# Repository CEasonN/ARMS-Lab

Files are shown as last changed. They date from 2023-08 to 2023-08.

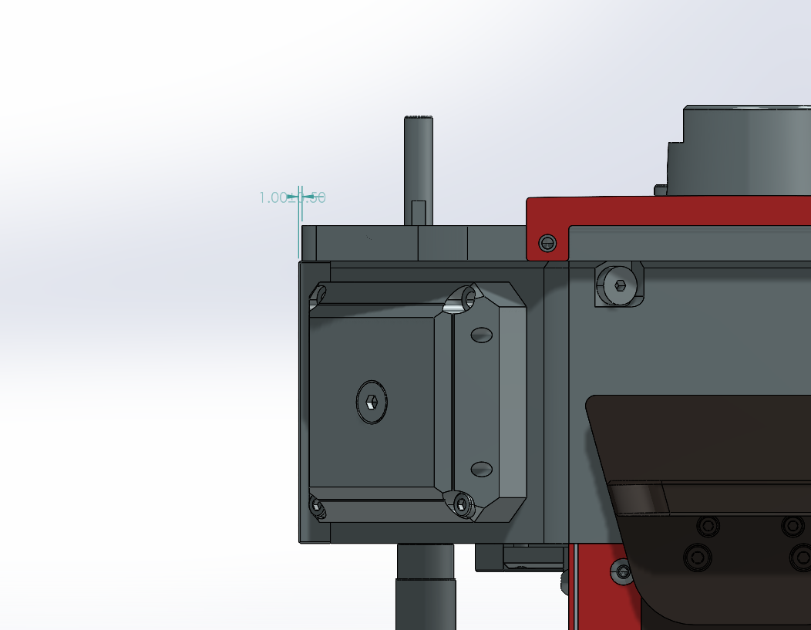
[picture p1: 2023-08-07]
SW screenshot/Annotation 2023-03-12 135321.png

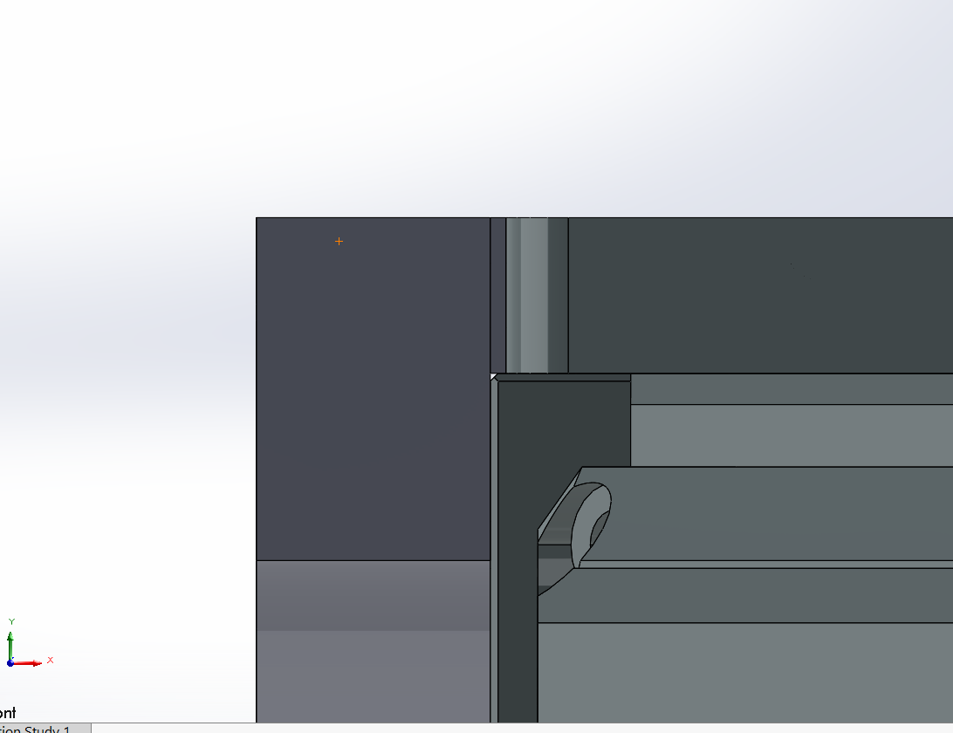
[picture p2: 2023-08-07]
SW screenshot/Annotation 2023-03-12 181023.png

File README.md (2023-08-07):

# ARMS-Lab
This experiment revolves around a height offset monitoring camera that records the directed energy deposition process. After the camera was installed, our graduate researchers observed some distortion in the camera’s images. They suspected that the distortion occurs as the heat from the deposition accumulates in the camera and its mounting apparatus.
Therefore, our objective is to characterize and quantify the heat transfer into the camera using an approximation for the clad temperature and clad area. We will then use these calculations to determine a failure condition for the camera and identify its critical component along with its thermal limit. Finally, we will validate our calculations by attaching thermocouples to the camera and conducting a circular deposition until a steady state response is reached. This constant heat addition will allow us to investigate a worst-case scenario for the camera. If necessary, a thermal management solution will be designed and implemented to mitigate overheating.

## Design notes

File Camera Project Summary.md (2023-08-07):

Height control camera thermal management project

# Summary
- Assess and characterize overheating problem on the the height control camera during maximum power continuous deposition.  
- Design and implement a minimum-complexity thermal management solution. 
- Validate solution performance under nominal conditions.

Secondary goal:
- Design enclosure for new IR raspberry pi camera
- Validate thermal performance under nominal conditions

# Resources to Start
- [height control methodology overview]("\ARMS_LAB\Publishing\2021\2021 Height Controller CIRP\CIRP 2021 - Soshi et al.pdf")
- [Vivian's thesis, details about camera mount design]("\ARMS_LAB\Forms and Documents\Thesises Dissertations\Vivian_Zhou_MSI_Thesis_2021.pdf")
- any heat transfer textbook for reference
- [visual height camera datasheet just the board](http://www.elpcctv.com/low-illumination-hd-usb-camera-module-aptina-ar0130-color-sensor-p-232.html)
- [visual height camera datasheet product](http://www.webcamerausb.com/elp-4mm-manual-focus-lens-aluminum-industrial-box-housing-960p-industrial-camera-p-214.html)

# Suggested To-Do List
1. Read Vivian's thesis, understand the thermal management problem
2. Create basic heat transfer model 
	1. Estimate clad irradiance 
	2. Estimate air cooling on enclosure
	3. Find expected lens and sensor equilibrium temperature
3. Instrument camera and design heating experiment
	1. Determine how to set temperature limits
4. Compare results to model
5. Determine cooling load required to not exceed required temperature
6. Begin solution design phase

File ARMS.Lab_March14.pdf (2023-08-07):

Masakazu Soshi
University of California Davis

## EME 199 WQ 2023: Undergraduate Research

Donjel Anthony Brox
Yizheng Chen

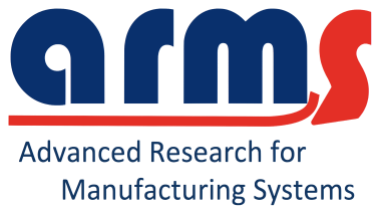
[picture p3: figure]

# Agenda

## - CCD Camera Thermal Management (CTM) Experiment - Substrate Manufacturing - Securing Current CCD Camera Fixture - New CCD Camera Fixture

# CTM Experiment: Description

## Problem:

- Current CCD camera overheats after ~170 thin-wall layers,

## causing the camera to turn off

## Solution: - Identify which part of the camera is overheating by attaching thermocouples to camera and performing depositions - Design thermal management solution to mitigate overheating

# CTM Experiment: Setup

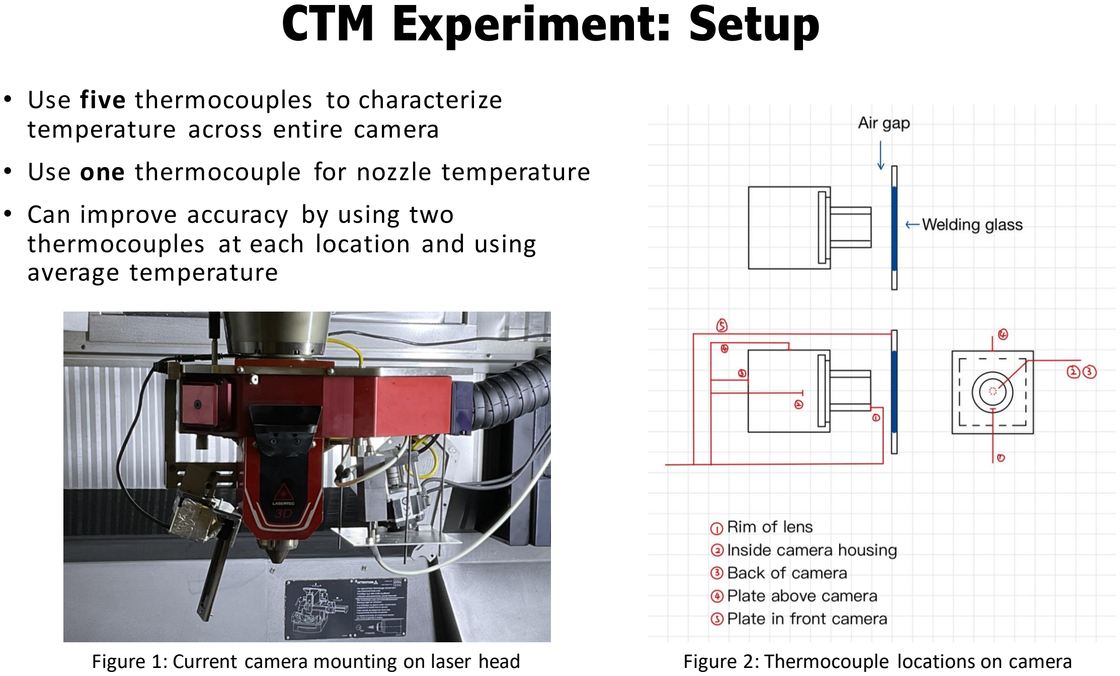
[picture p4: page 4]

- Use five thermocouples to characterize temperature across entire camera
- Use one thermocouple for nozzle temperature
- Can improve accuracy by using two thermocouples at each location and using average temperature
Figure 1: Current camera mounting on laser head | Figure 2: Thermocouple locations on camera

# CTM Experiment: Depositions

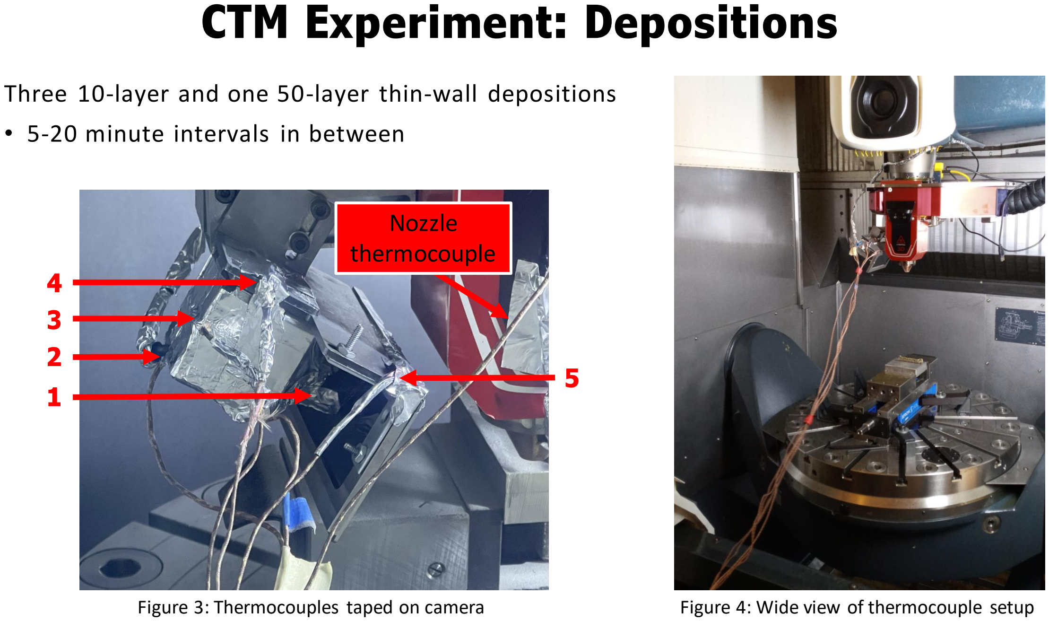
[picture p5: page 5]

Three 10-layer and one 50-layer thin-wall depositions
- 5-20 minute intervals in between
Figure 3: Thermocouples taped on camera | Figure 4: Wide view of thermocouple setup

1

3
2

4

5

Nozzle
thermocouple

# CTM Experiment: Temperature Data

Observations:
- Camera is protected by shield, but slowly heats up from shield radiating absorbed heat
- Shield temperature increases linearly then drops slowly after deposition ends
- Due to internal cooling, the nozzle has a controlled, oscillating temperature

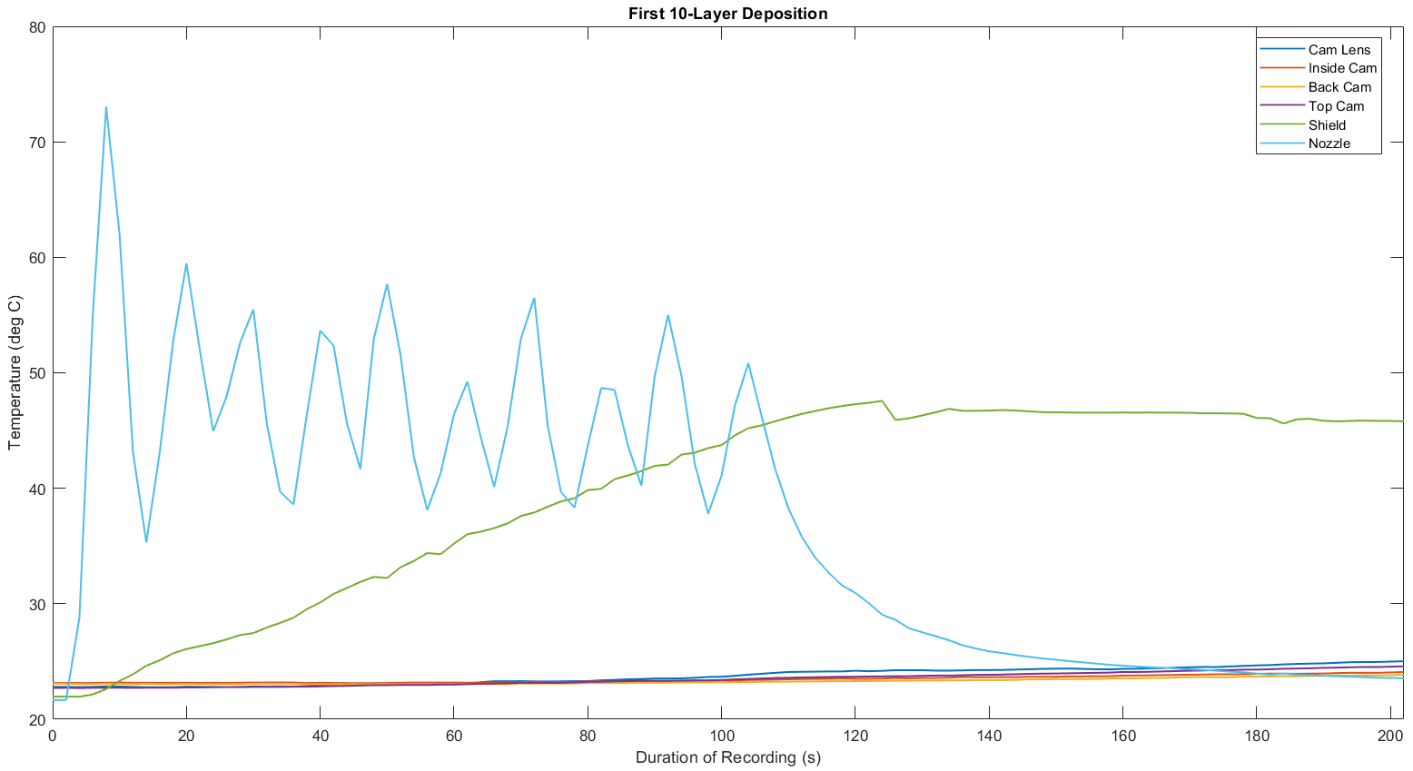
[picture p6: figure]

# CTM Experiment: Temperature Data

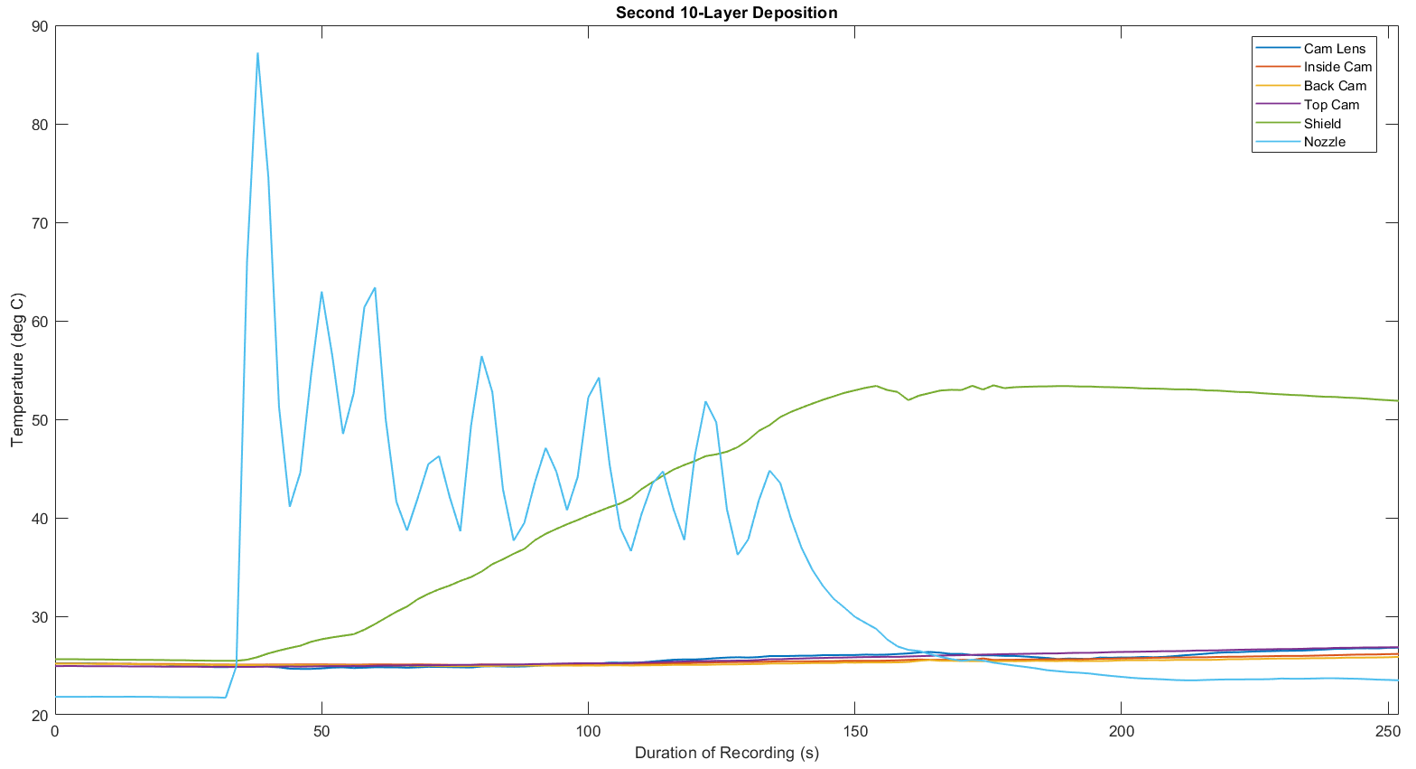
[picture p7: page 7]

# CTM Experiment: Temperature Data

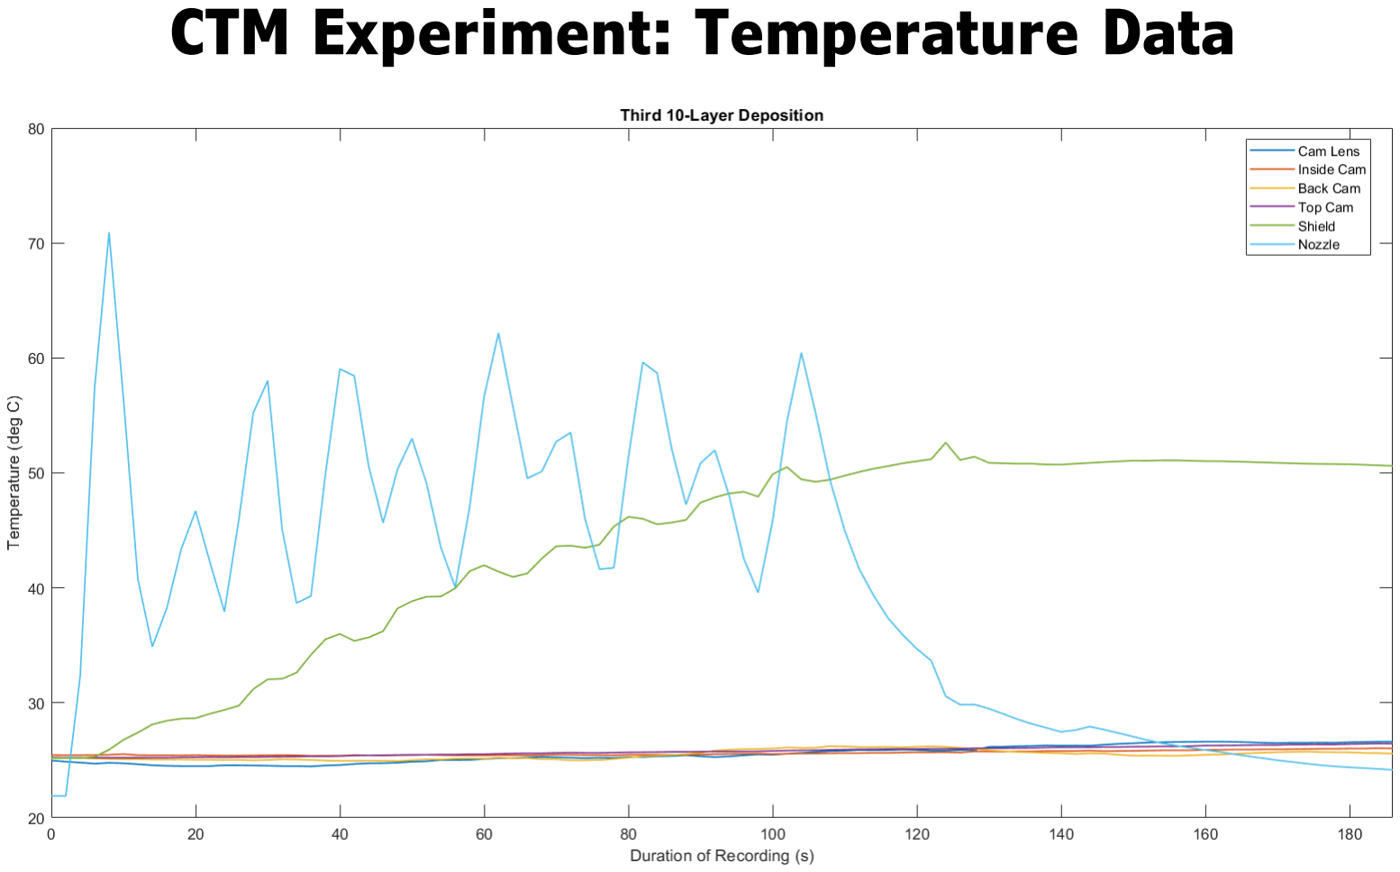
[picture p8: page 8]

Observations:
- Incomplete data for shield since DAC temperature range not set high enough
- Camera is protected by shield, but slowly heats up from shield radiating absorbed heat
- Shield temperature increases linearly then drops slowly after deposition ends
- Due to internal cooling, the nozzle has an oscillating temperature that slowly increases

# CTM Experiment: Temperature Data

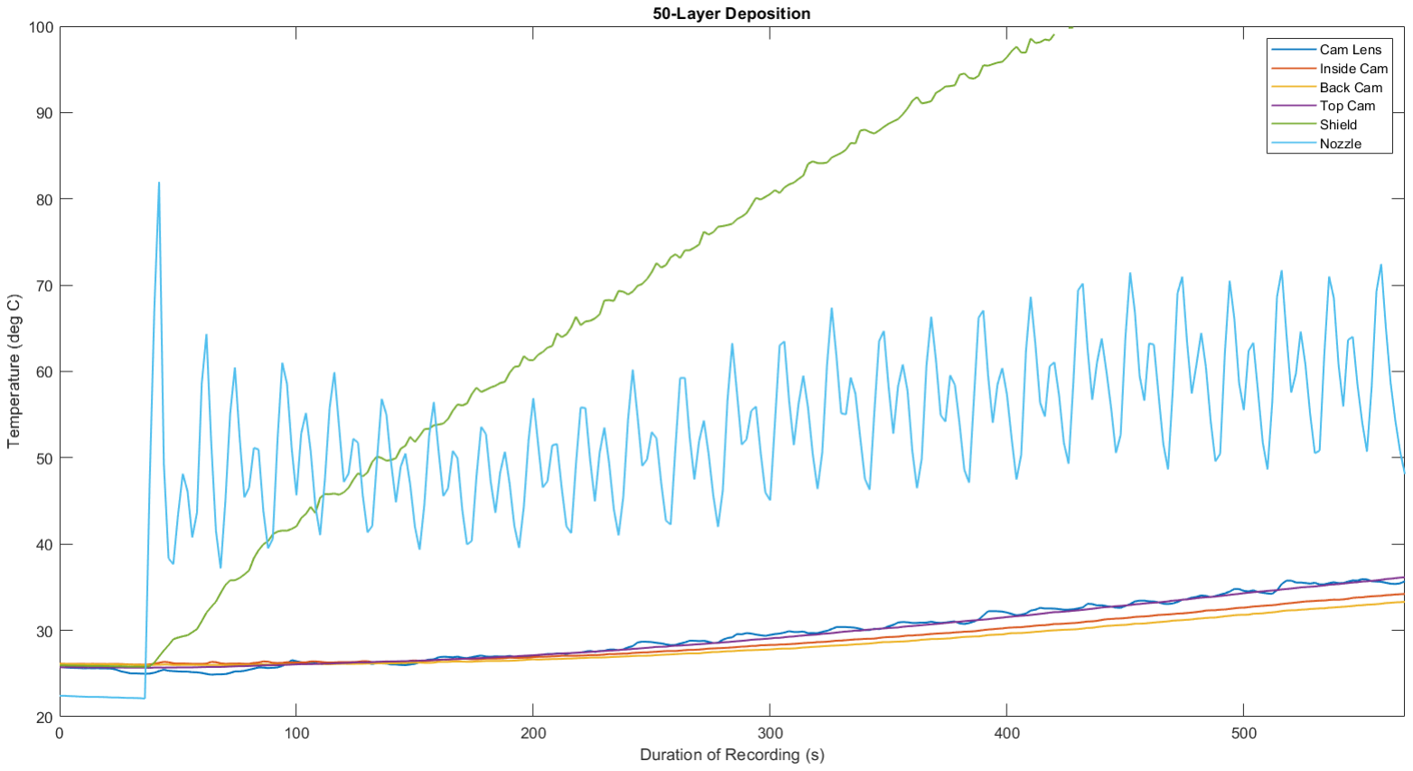
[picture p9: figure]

Observations:
- Camera slowly heats up after deposition due to shield radiating heat absorbed earlier
- Nozzle drops to room temperature quickly after deposition ends, at which point the camera is only being heated by the shield

# CTM Experiment: Temperature Data

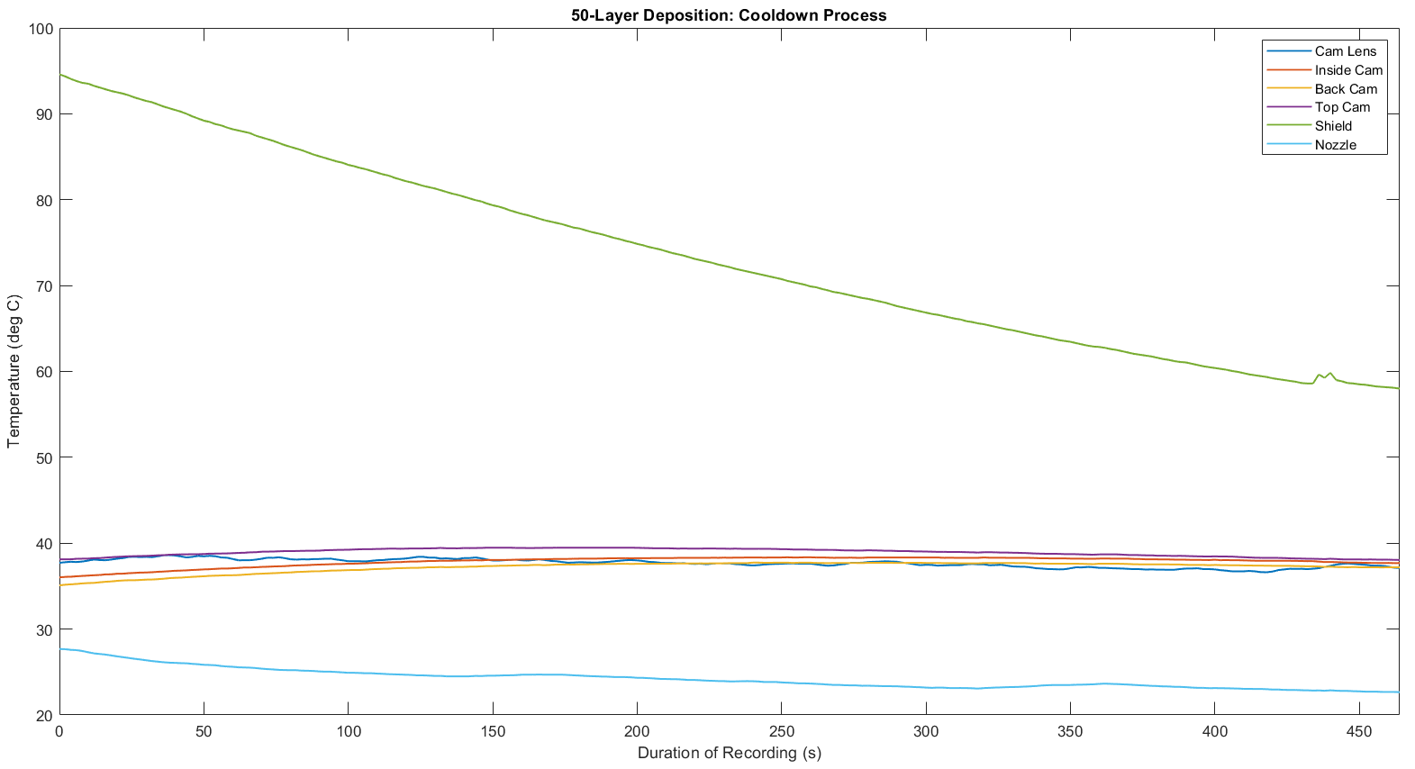
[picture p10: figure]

# CTM Experiment: Analysis

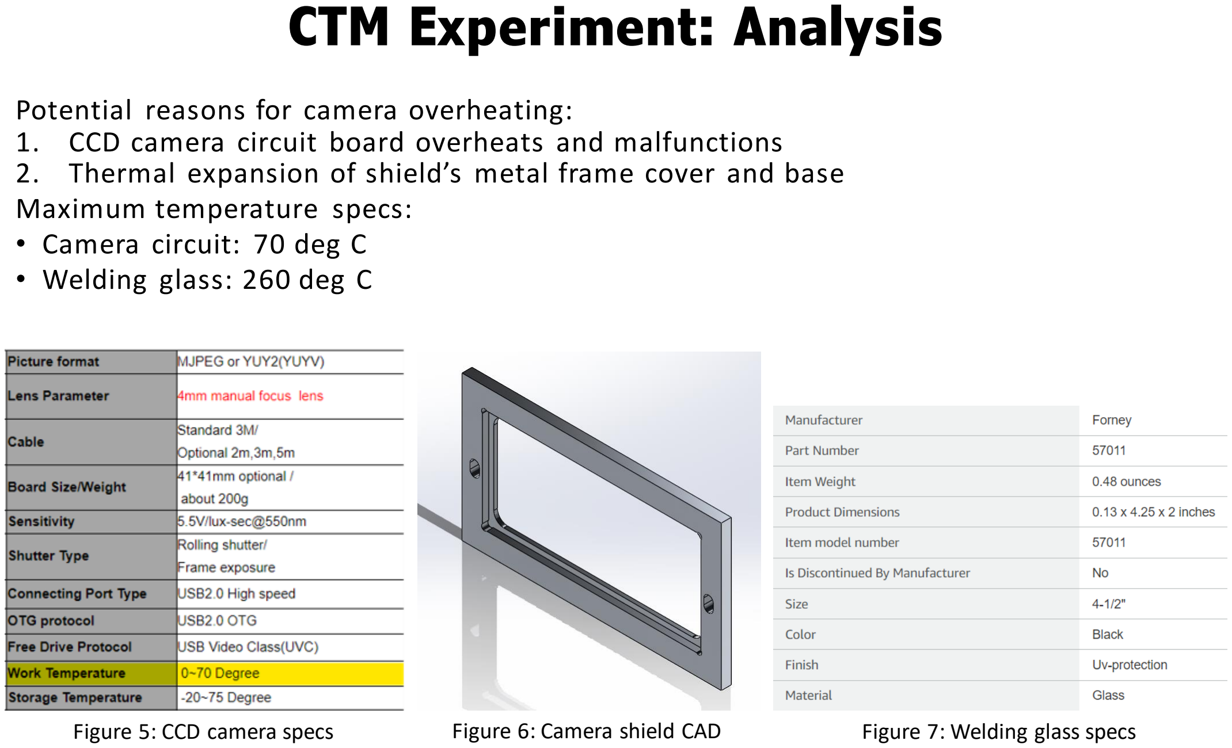
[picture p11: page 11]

Potential reasons for camera overheating:
1. CCD camera circuit board overheats and malfunctions
2. Thermal expansion of shield’s metal frame cover and base Maximum temperature specs:
- Camera circuit: 70 deg C
- Welding glass: 260 deg C
Figure 5: CCD camera specs | Figure 6: Camera shield CAD | Figure 7: Welding glass specs

## Takeaways from experimental data and equipment specs: - Use curve fitting to estimate shield and camera temperature after any number of layers

- Allows us to estimate when the camera will fail, which we’ll use to determine thermal management solution
- Among all camera thermocouples, use camera lens data for curve fitting since it reads highest temperatures and absorbs most heat

# CTM Experiment: Data Analysis

# CTM Experiment: Data Analysis

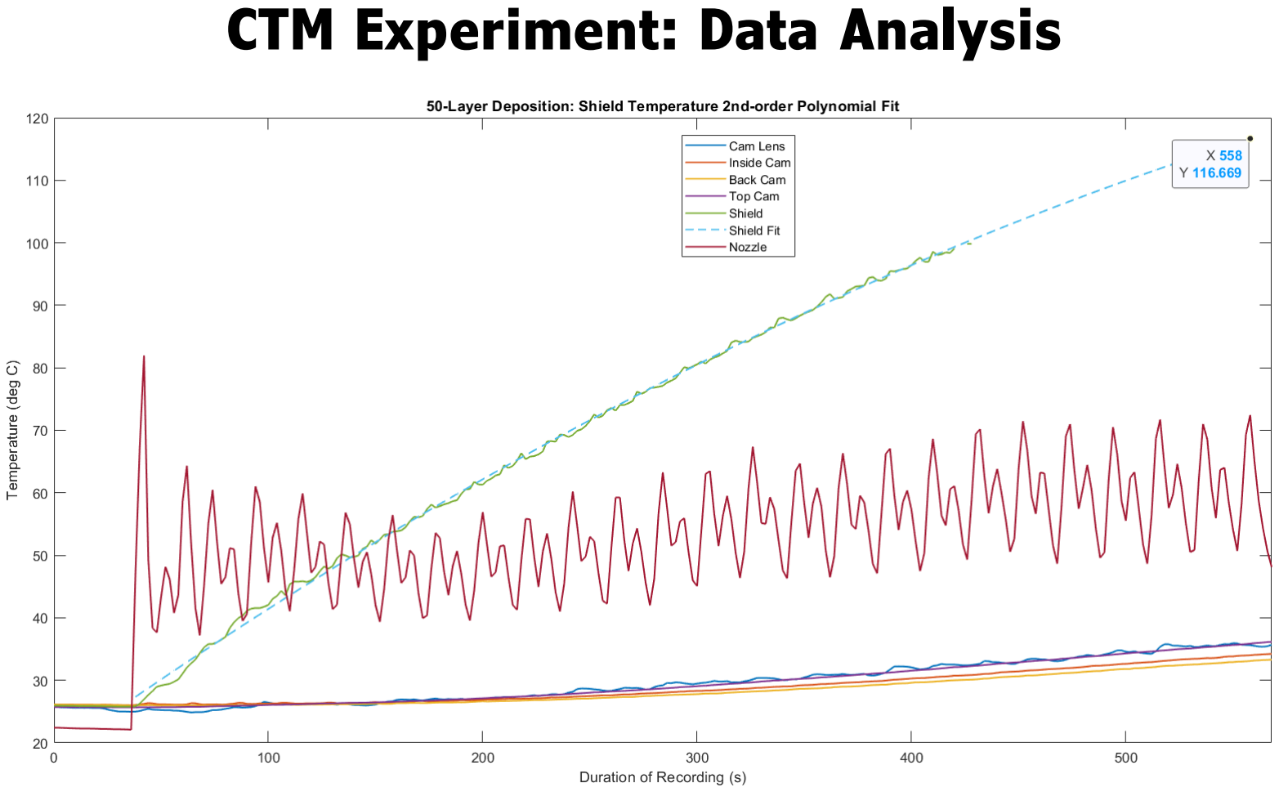
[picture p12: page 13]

The shield is predicted to have reached 116 deg C after 50 layers.

# CTM Experiment: Data Analysis

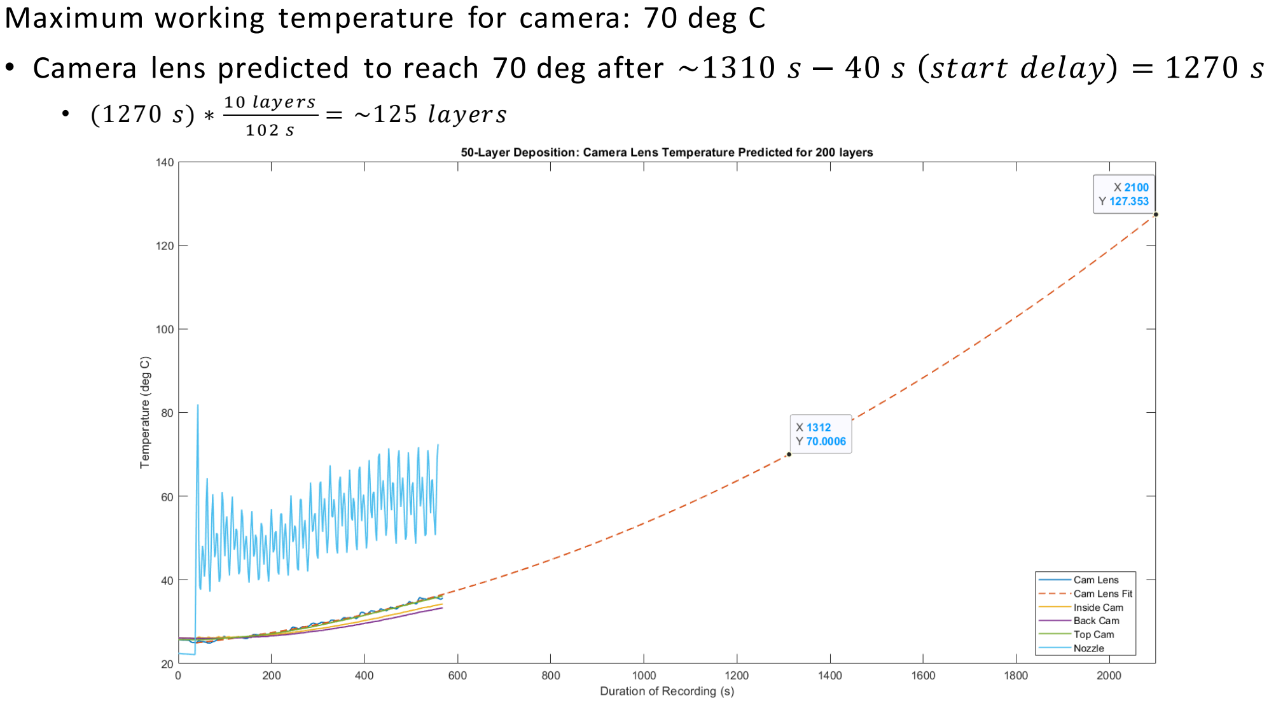
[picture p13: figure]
10 laye rs; = ~125 layers

Maximum working temperature for camera: 70 deg C
- Camera lens predicted to reach 70 deg after ~1310 s − 40 s start delay = 1270 s

Investigate whether heat sinks will suffice by quantifying theoretical heat dissipation provided
- Geometry constraints: plates above camera constrain heat sink to 129 x 36 mm area
- Optimize heat dissipation performance by developing MS Excel sheet
Investigate if a larger air gap between camera and shield provides sufficient insulation

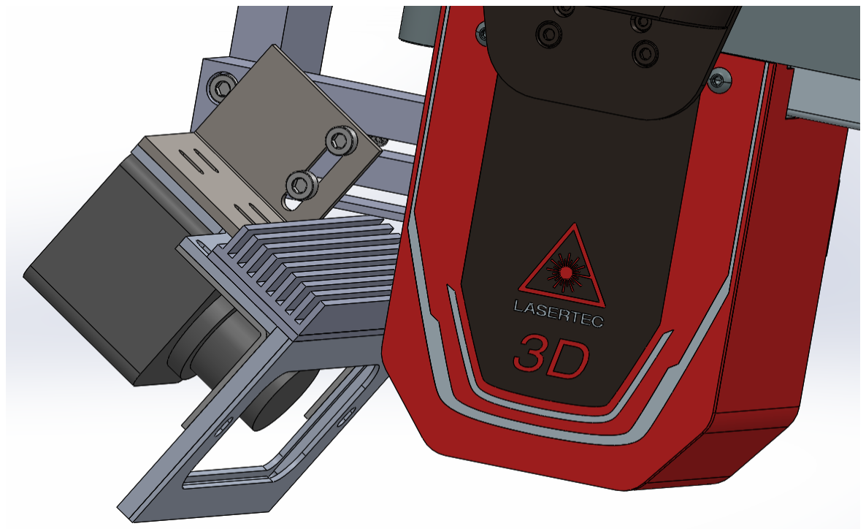
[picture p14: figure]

Figure 8: CAD draft of heat sink atop CCD camera shield

# CTM Experiment: Thermal Management

# Substrate Manufacturing

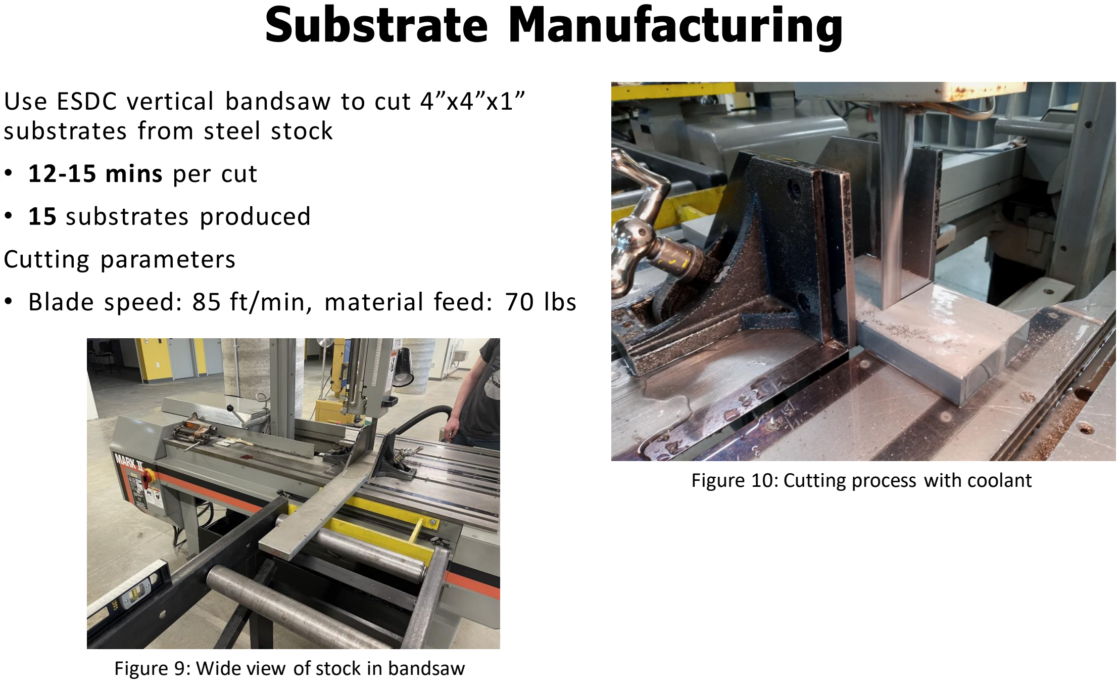
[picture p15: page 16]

Use ESDC vertical bandsaw to cut 4”x4”x1” substrates from steel stock
- 12-15 mins per cut
- 15 substrates produced
Cutting parameters
- Blade speed: 85 ft/min, material feed: 70 lbs

Figure 9: Wide view of stock in bandsaw

Figure 10: Cutting process with coolant

# Securing Current CCD Camera Fixture

Problem:
- Screwing the fixture into the laser head causes fixture to tilt, making the camera position inaccurate each time it’s installed
- Issue is due to laser head not being flush with fixture (see Figure 11)
Possible solutions:
- L-shaped metal piece
- Fixes fixture in a new plane, preventing rotation
- Thin metal spacer
- Fills the space in between the laser head and fixture, making them flush

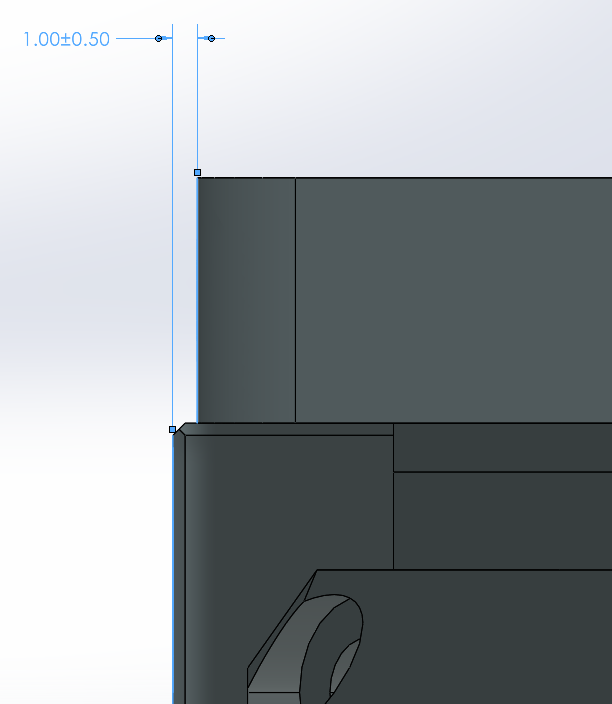
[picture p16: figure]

Figure 11: 1mm discrepancy on laser head mating face

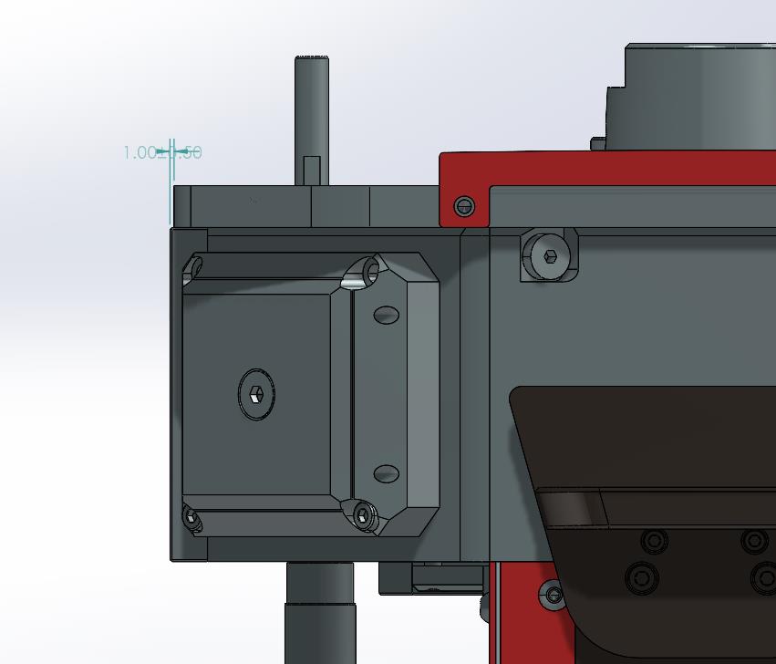
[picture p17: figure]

Figure 12: 1mm discrepancy on laser head mating face (zoomed out)

# Current CCD Camera Fixture: Spacer

# Current CCD Camera Fixture: Spacer

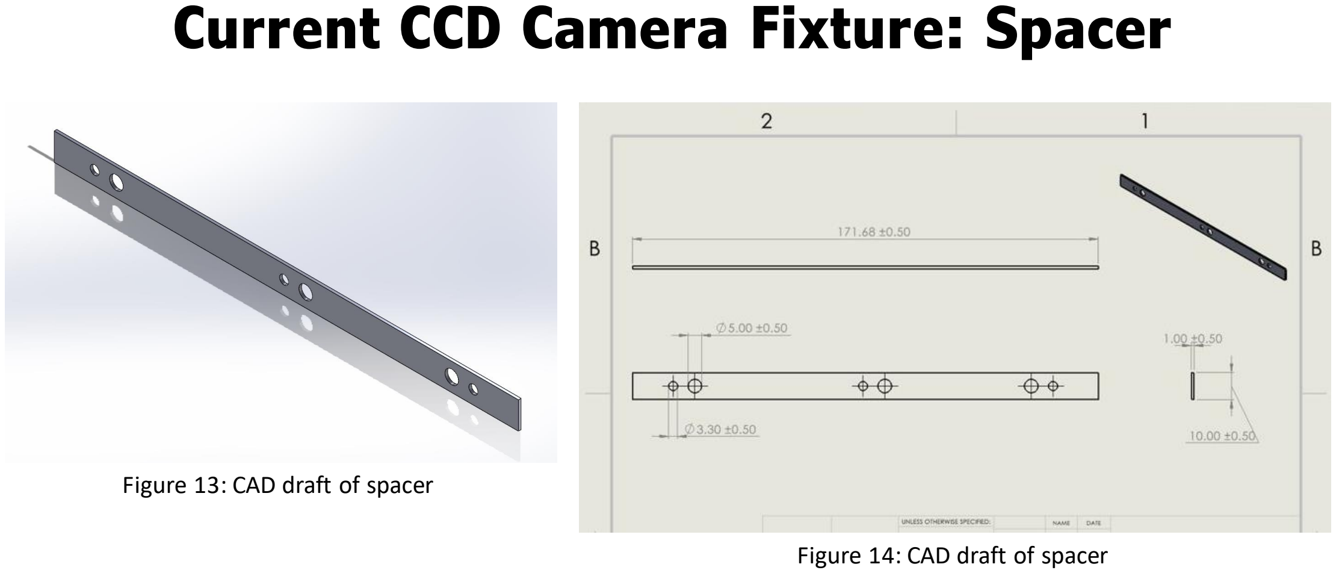
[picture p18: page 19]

Figure 13: CAD draft of spacer

Figure 14: CAD draft of spacer

# Current CCD Camera Fixture: Spacer

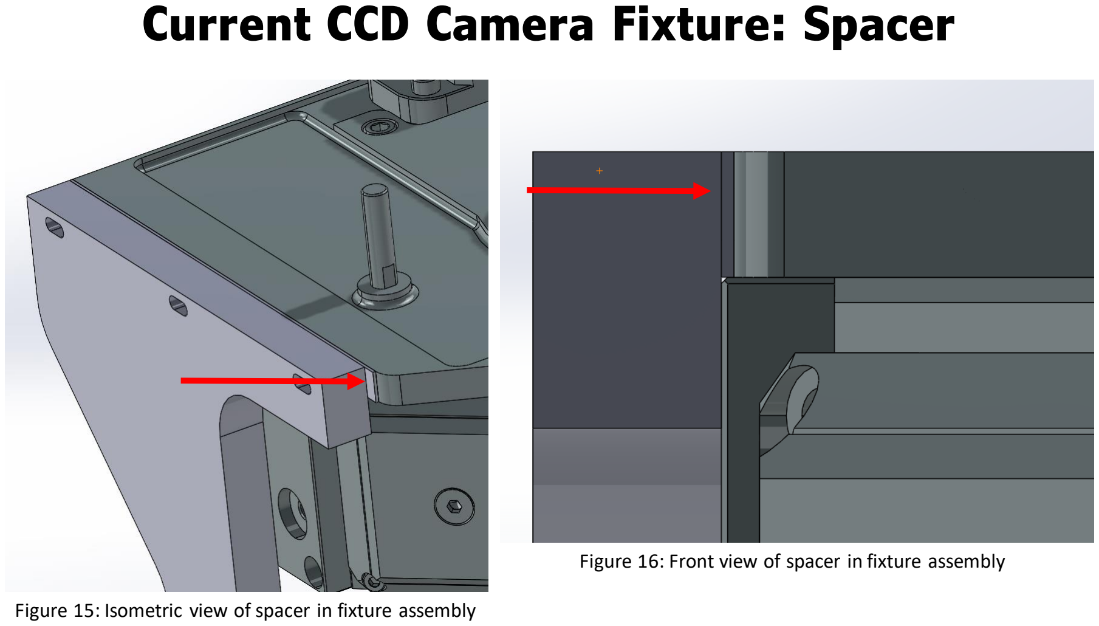
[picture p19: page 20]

Figure 15: Isometric view of spacer in fixture assembly

Figure 16: Front view of spacer in fixture assembly

# Current CCD Camera Fixture: Angle Bracket

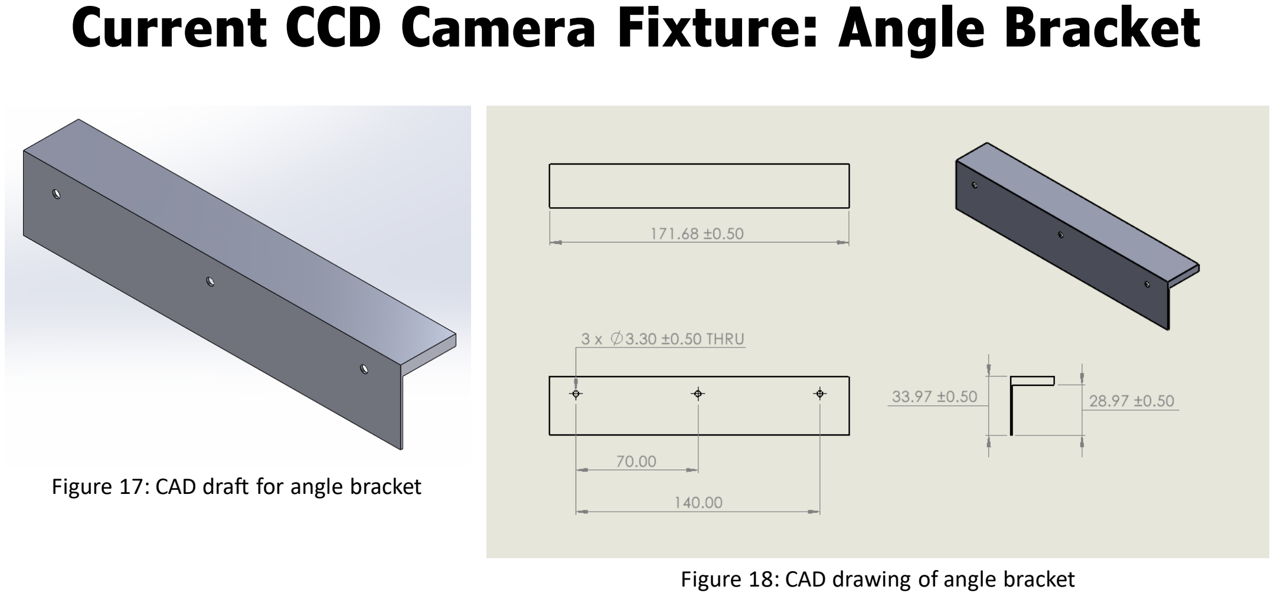
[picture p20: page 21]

Figure 17: CAD draft for angle bracket

Figure 18: CAD drawing of angle bracket

# Current CCD Camera Fixture: Angle Bracket

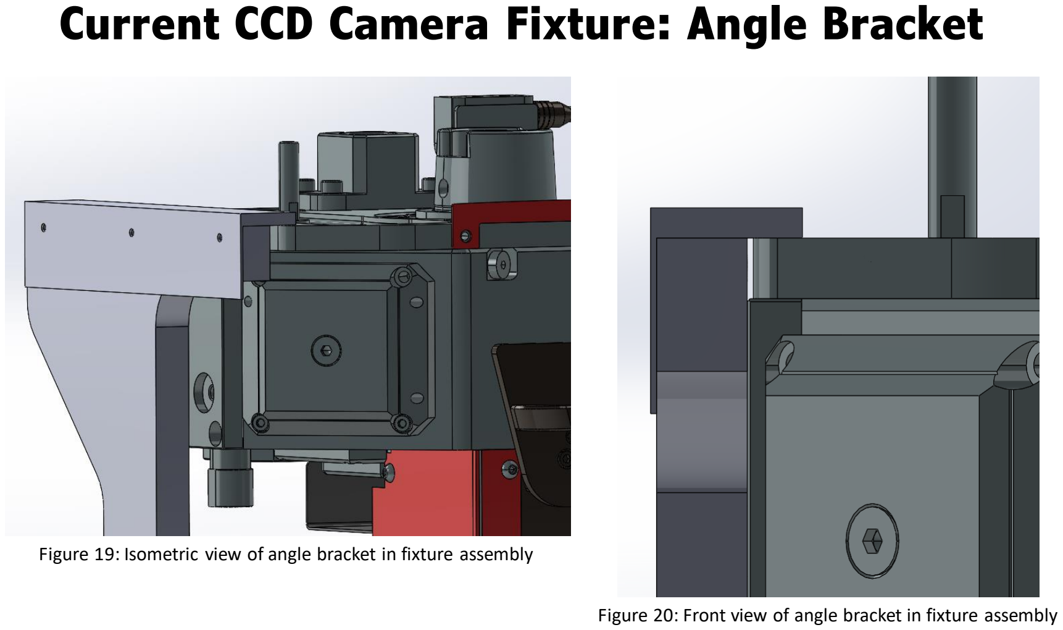
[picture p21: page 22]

Figure 19: Isometric view of angle bracket in fixture assembly

Figure 20: Front view of angle bracket in fixture assembly

# New CCD Camera Fixture: Fixture Points

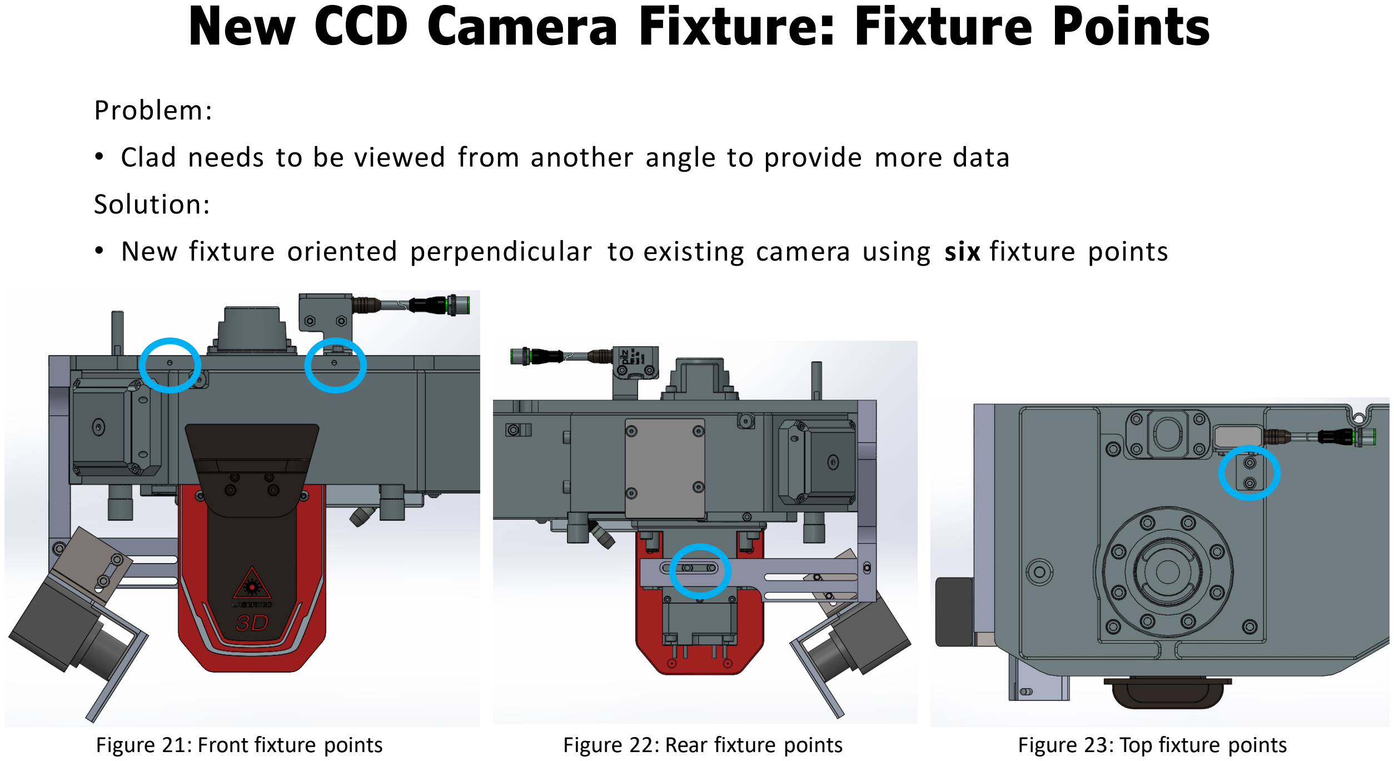
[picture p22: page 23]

Problem:
- Clad needs to be viewed from another angle to provide more data
Solution:
- New fixture oriented perpendicular to existing camera using six fixture points
Figure 21: Front fixture points | Figure 22: Rear fixture points | Figure 23: Top fixture points

# New CCD Camera Fixture: Draft Assembly

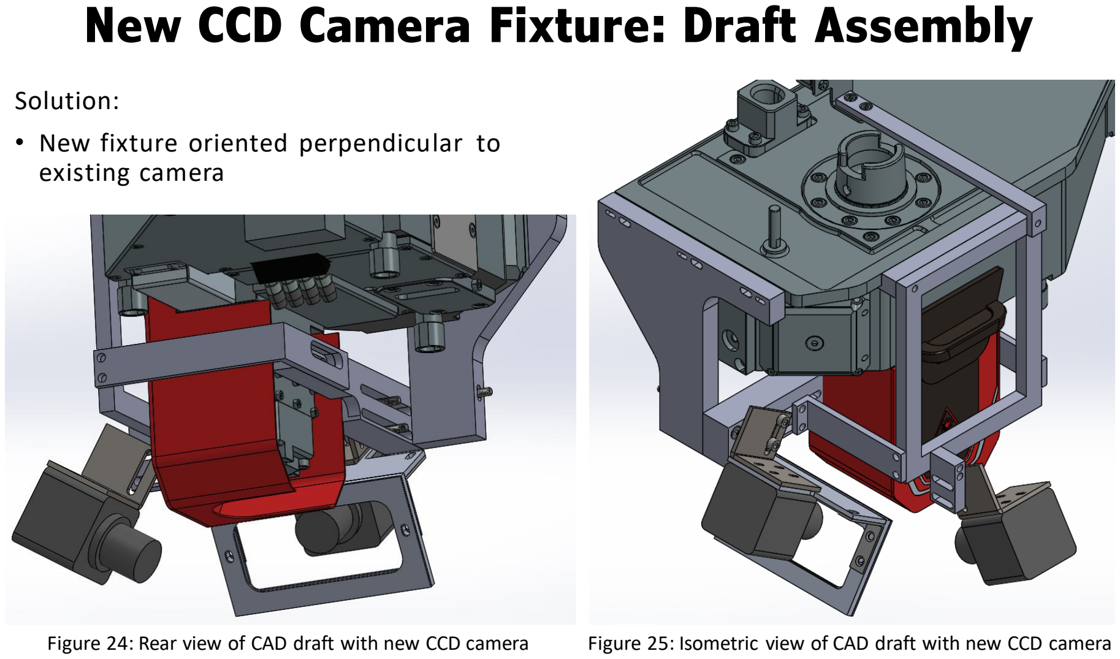
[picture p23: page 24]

Solution:
- New fixture oriented perpendicular to existing camera

Figure 24: Rear view of CAD draft with new CCD camera Figure 25: Isometric view of CAD draft with new CCD camera

# Future Work

## Experiment - Finish analysis of results

- Research properties of welding glass and temperature tolerances of camera

## - Continue designing thermal management solution - Manufacture/order and implement solution - Perform CFD and/or FEA analysis on working solution - Write report on finished solution

## Continue developing current CCD camera fixture addition and new CCD camera fixture

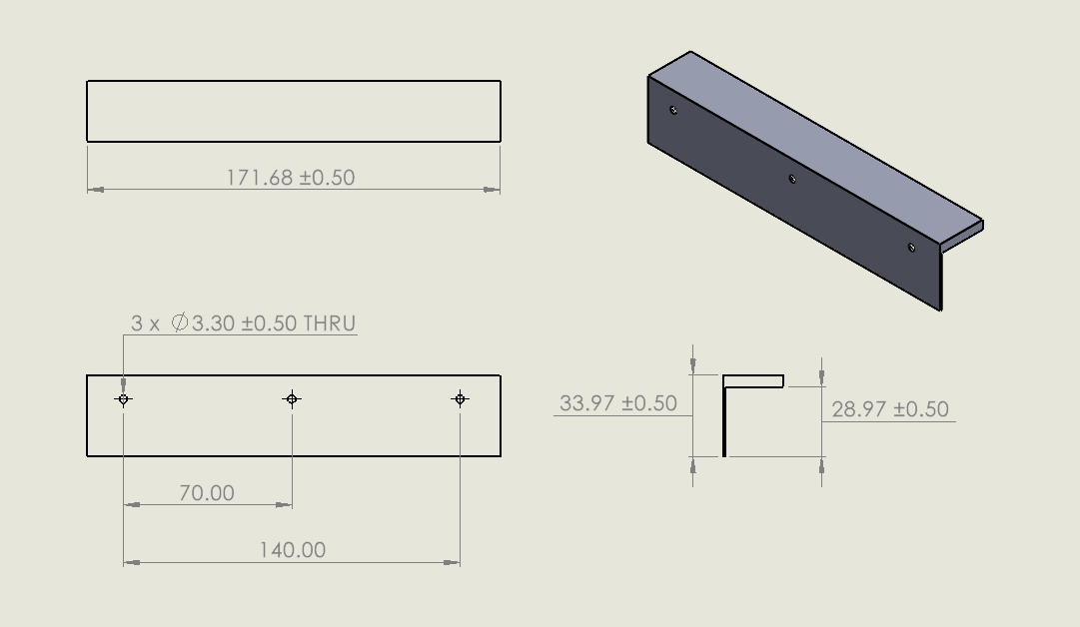
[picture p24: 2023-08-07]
SW screenshot/Annotation 2023-03-12 184950.png

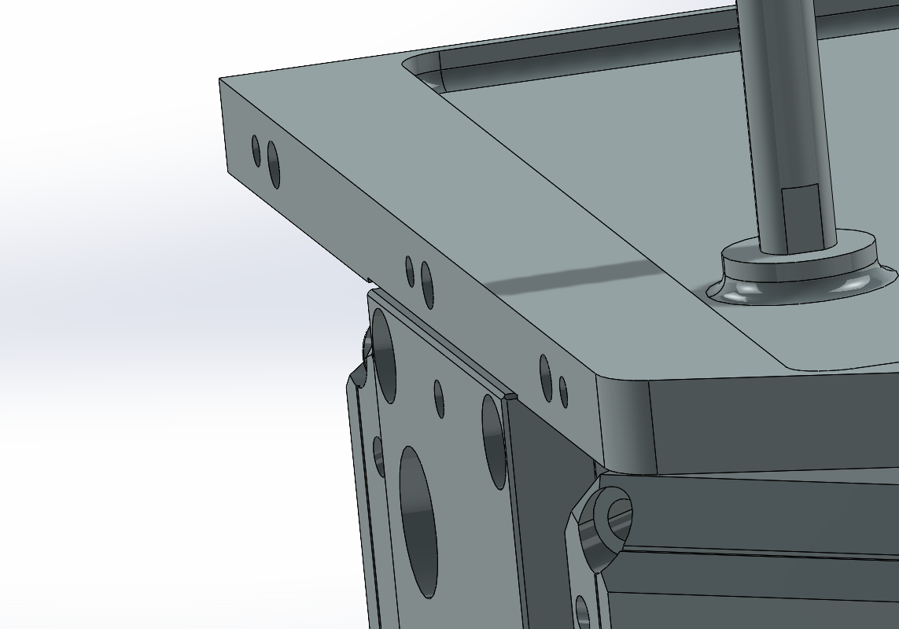
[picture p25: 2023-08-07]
SW screenshot/Annotation 2023-03-12 153420.png

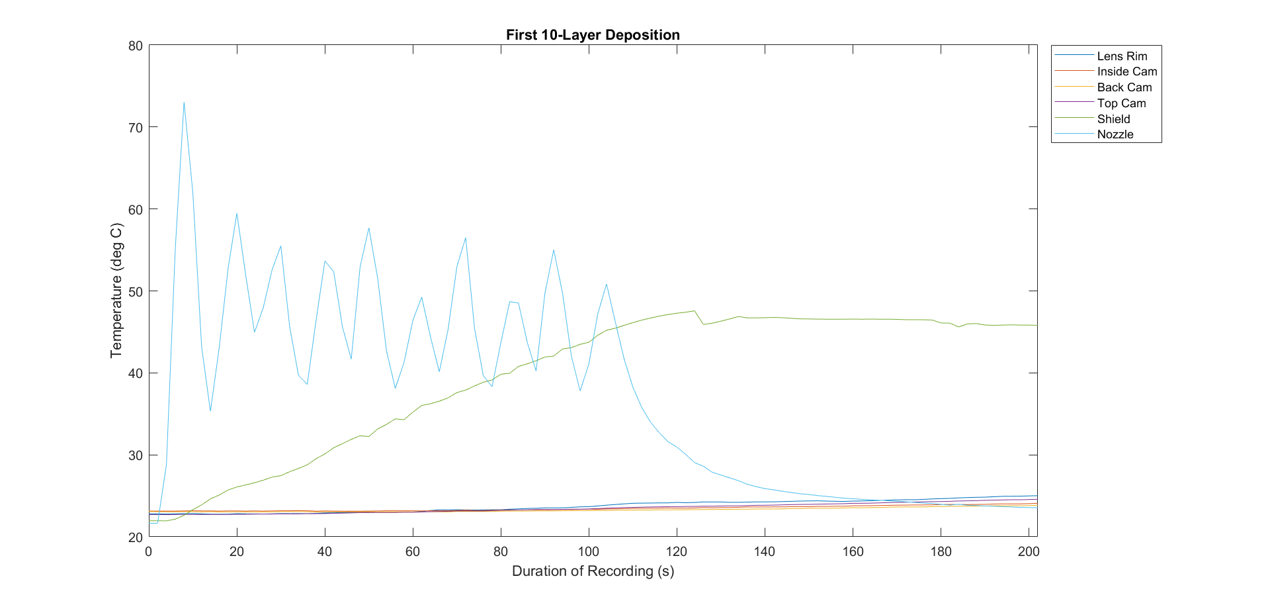
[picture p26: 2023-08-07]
Plots/1st_10Layer.png

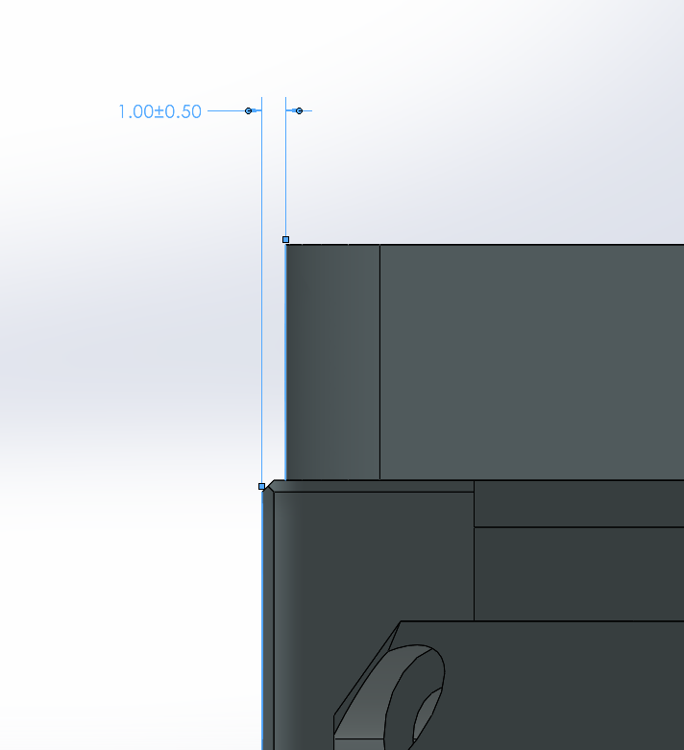
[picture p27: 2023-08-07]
SW screenshot/Annotation 2023-03-12 135355.png

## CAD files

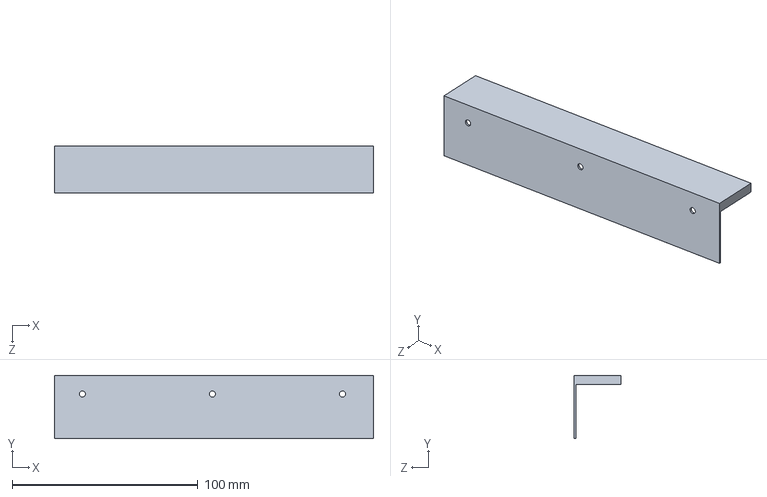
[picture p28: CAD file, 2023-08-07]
Lblock.SLDPRT
171.7 x 34.0 x 25.2 mm

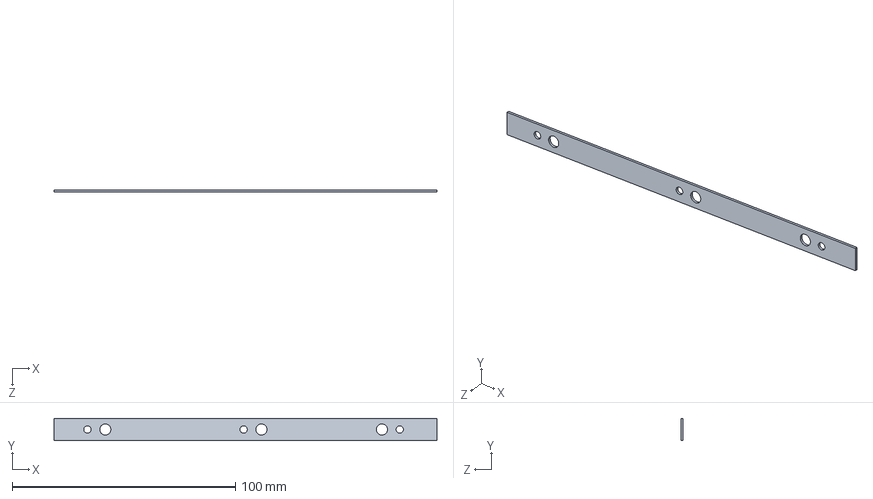
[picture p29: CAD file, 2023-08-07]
spacer.SLDPRT
171.7 x 10.0 x 1.00 mm

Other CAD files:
Lblock.SLDDRW
spacer.SLDDRW

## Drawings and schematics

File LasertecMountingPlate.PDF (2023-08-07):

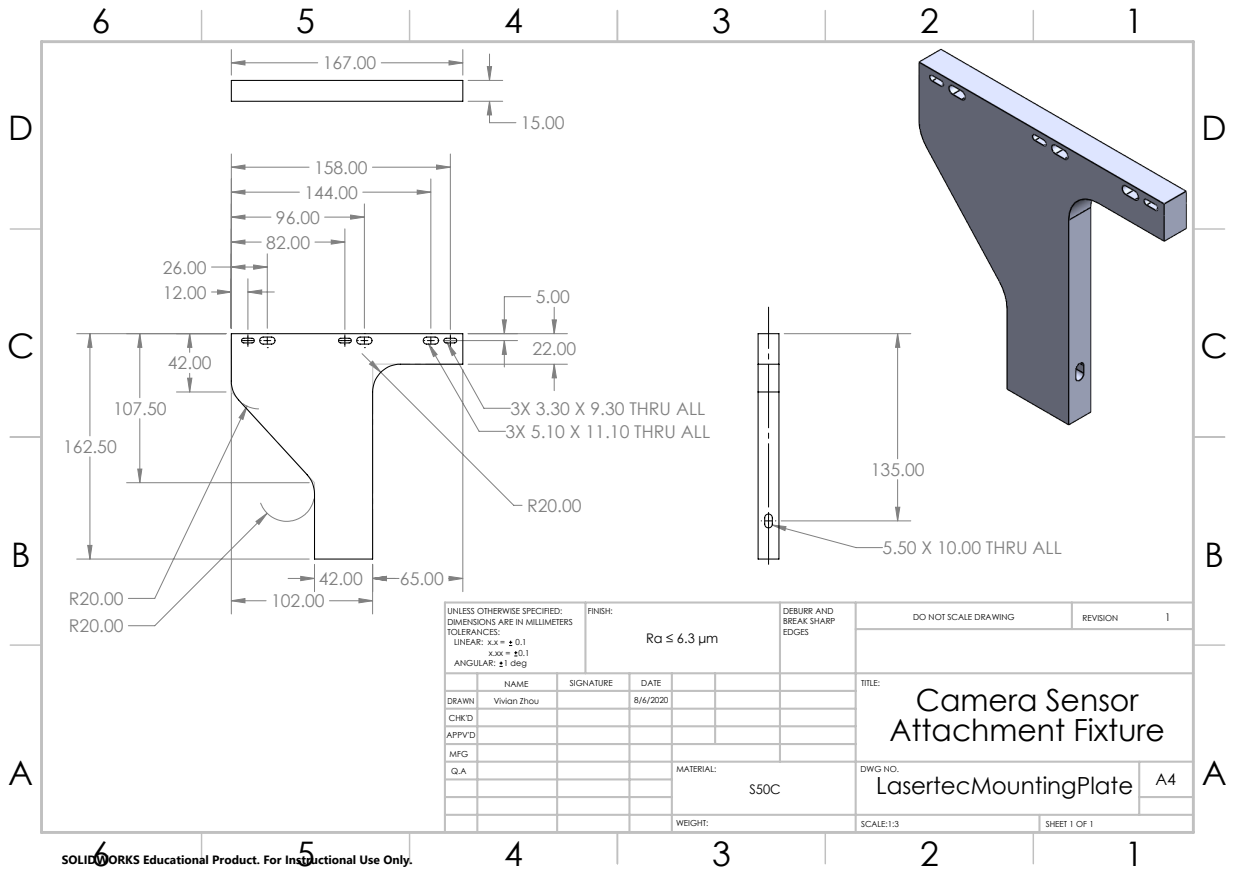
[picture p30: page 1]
3X 5.10 X 11.10 THRU ALL; 3X 3.30 X 9.30 THRU ALL; 5.50 X 10.00 THRU ALL; FINISH:; DEBURR AND; BREAK SHARP; DO NOT SCALE DRAWING; REVISION; SCALE:1:3; SHEET 1 OF 1

UNLESS OTHERWISE SPECIFIED:
DIMENSIONS ARE IN MILLIMETERS
TOLERANCES:
LINEAR: x.x = 0.1
ANGULAR: 1 deg

NAME | SIGNATURE | DATE | | | | TITLE: Camera Sensor Attachment Fixture

DRAWN | Vivian Zhou | | 8/6/2020
CHK'D
APPV'D
MFG
Q.A | | | | MATERIAL: S50C | DWG NO. LasertecMountingPlate | A4

SOLIDWORKS Educational Product. For Instructional Use Only.
